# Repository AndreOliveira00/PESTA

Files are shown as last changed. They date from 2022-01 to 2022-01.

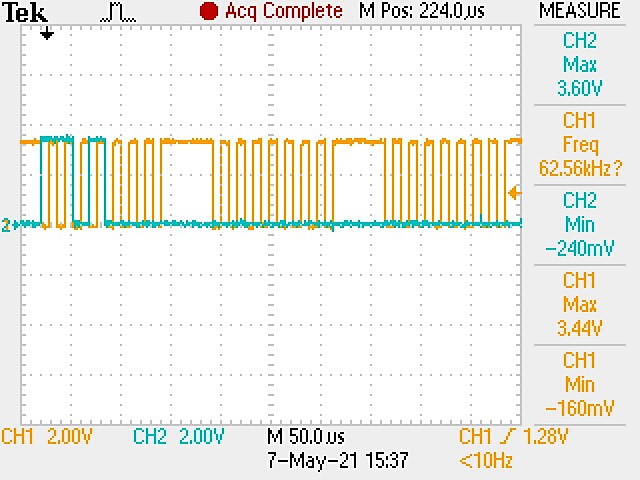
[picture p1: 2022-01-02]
Tests/SPI communication/MOSI/GetStatus_1.JPG

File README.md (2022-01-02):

# Skylight Control System
SISTEMA DE  CONTROLO DO MOVIMENTO DE UMA CLARABOIA

Este repositório contem o relatório e poster ilustrativo do projeto desenvolvido durante o estágio de fim de Licenciatura em Engenharia Eletrotécnica e de Computadores pelo Instituto Superior de Engenharia do Porto.
Contem ainda parte do código desenvolvido em: 
"...STM32CubeExpansion_SPN3\Projects\Multi\Examples\MotionControl\IHM03A1_ExampleFor1Motor" para controlo de todos os dispositivos incorporados na rede daisy chain.
Imagens ilustrativas da PCB final, o seu desenvolvimento associado e alguns testes efetuados para validação da comunicação SPI, teste de circuitos, respostas temporais, EMI e obtenção de constantes motoras.
Preço do desenvolvimento das duas PCBs associadas

RESUMO DO PROJETO:

O projeto apresentado neste documento consiste num sistema embebido para controlo de abertura e fecho de uma claraboia incorporada no tejadilho dos autocarros. A solução desenvolvida procurou a adaptabilidade a diferentes veículos, pelo que permitirá o controlo por parte do utilizador, sem maiores dificuldades, seguindo assim o conceito de Smart City.
O sistema visa a robustez sendo implícito a implementação das boas práticas Electromagnetic compatibility (EMC) e cumpridor da norma UNECE R10 no momento de dimensionamento do hardware associado. Os testes ao sistema desenvolvido foram feitos num laboratório isolado, com alimentação de uma bateria externa, com recurso a um analisador de espetro e sondas EMC.
O movimento rotativo do motor passo a passo NEMA 23 encontra-se acoplado com uma engrenagem módulo 1,5 capaz de elevar a estrutura por 7 cm. Este movimento é visível nos dois extremos da claraboia com auxílio de dois motores, sendo esta estrutura rígida.
O dispositivo de controlo principal é constituído por um microcontrolador Advanced RISC Machine (ARM) Cortex M4 de 32 bits, o STM32F401RET6 baseado numa arquitetura Reduced Instruction Set Computer (RISC), responsável por controlar os dois drivers junto 
dos referidos motores. Estes drivers incorporam um dispositivo de comando das fases, o powerSTEP01, com controlo programável através de Serial Peripheral Interface (SPI).
A comunicação entre o dispositivo principal e os drivers é feita através do protocolo de comunicação SPI segundo uma topologia em daisy chain atuando este primeiro como mestre e os restantes como escravos. Adicionalmente foi alvo de estudo a necessidade de 
implementação de uma comunicação RS-485 entre os dois escravos fruto de um sistema funcional num ambiente sujeito a ruído eletromagnético.

Para outros esclarecimentos contacte pelo email 1181045@isep.ipp.pt.

Notas:
  O desenvolvimento do software foi feito em: "...STM32CubeExpansion_SPN3\Projects\Multi\Examples\MotionControl\IHM03A1_ExampleFor1Motor"

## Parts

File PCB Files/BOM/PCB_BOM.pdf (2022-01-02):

# Bill of Materials

2175 Salk Avenue
Project Title: Bill of Materials for PCB Document [PCB2.PcbDoc] | Suite 200
Project File Name: Claraboia.PrjPcb | Carlsbad, CA 92008
Assembly Variant: None | USA
Part Number | Description | Designator | Manufacture | Manufacture Part Number | Supplier | Supplier Part Number | Supplier Unit Price | Quantity
S8B-EH_LF__SN_ | Conector Femea 1*8 90 graus | 485-1 | | | | | | | 1
CMP-02366-000003-1 | CONN MOD JACK 8P8C R/A UNSHLD | 485-2, 485-4 | | | | | | | 2
S8B-EH_LF__SN_ | Conector Femea 1*8 90 graus | 485-3 | | | | | | | 1
CMP-2100-03601-2 | CAP CER 0.1UF 50V X7R 0603 | C1, C2, C3, C4, C6, C9, C16, C17, C18, C19, C20, C21, C22, C23, C24, C36, C37, C39 | | | | | | 18
CMP-06035-019733-1 | Cap Ceramic 4.7uF 50V X5R ±10% SMD 0805 +85°C Emboss T/R | C5, C10, C44 | | | | | | | 3
CMP-2000-07203-1 | Tantalum Surface Mount Capacitor, 4.7 uF, +/- 20%, 50 V, -55 to 125 degC, 2-Pin SMD, RoHS, Tape and Reel T491D475M050AT | C7 | | | | | | | 1
CMP-06035-005015-1 | Chip Multilayer Ceramic Capacitors for General Purpose, 0805, 10uF, X5R, 15%, 10%, 50V GRM21BR61H106KE43K | C8 | | | | | | | 1
CMP-2006-02448-10603 | | C11, C12 | | | | | | | 2
CMP-2006-04264-1 | | C13, C14, C42, C43 | | | | | | | 4
CMP-1035-02737-2CAP CER 1UF 16V X5R 0603 CMP-0687-00076-1 | Aluminum Electrolytic Capacitor, UD Series, Low Impedance, 68 uF, 50 V, + / -20%, -55 to 105 degC, Chip Type, 8 x 10 mm D x L, Pb-Free, Reel UUD1H680MNL1GS | C15 C25, C26 | | | | | | | 1 2
EEU-FC1H680B | Capacitor Polarised | C27, C28 | | 2
CMP-1036-04552-2 | CAP CER 0.22UF 50V X7R 0805 | C29, C30, C31, C32, C33, C40 | | 6
CMP-13271-004199-1 | CL21 Series 0805 47nF 50V ±5% Tolerance X7R Multilayer Ceramic Chip Capacitor | C34 | | 1
CMP-2006-02821-1470 nF | | C35, C38 | | 2
T495A226K006ATE500 | Capacitor Polarised 22 uF TANT | C41 | | 1
CMP-0548-00185-2 | Transient Voltage Suppressor, 6.40 to 231 V, 30 V Stand-off Voltage, Bi-Directional, -55 to 155 degC, 2-pin DO-214AC, Pb-Free, Tape and Reel | D1, D3, D5, D8, D9, D10, D11, D14, D15, D16, D17, D18, D19, D30, D31 | 15
BAT760Q-7 | No Description Available | D2, D4, D6 | | 3
CMP-1426-00009-1 | SMD mono-color Chip LED, WL-SMCW, Bright Green | D7, D27 | | 2
CMP-1426-00012-1 | SMD mono-color Chip LED, WL-SMCW, Yellow | D12, D13, D20, D21, D22, D23 | | 6
CMP-2000-05915-2 | DIODE ARRAY SCHOTTKY 30V SOT23-3 | D24 | | 1
CMP-02539-000007-1 | DIODE SCHOTTKY 100V 150MA SOD123 | D25, D26 | | 2
CMP-1426-00011-1 | SMD mono-color Chip LED, WL-SMCW, Red | D28, D29 | | 2
CMP-1060-00535-1 | Zener Voltage Regulator, 500 mW, 2-Pin SOD-123, Pb-Free, Tape and Reel | D32 | | 1
MFU1206FF00500P100 Fuse | | F1 | | 1
MMZ1608S601ATD25 Ferrite Bead CMP-0225-00066-1 | Radial Leaded Wire Wound Inductor WE-TI, L = 4700 µH 7447721047 | FB1 L1 | | 1 1
P78E03-1000 | Connector | P1 | 1
M50-3530642 | Connector | P2 | 1
OSTYK42106030 CMP-1502-01064-1 | Connector THT Vertical Pin Header WR-PHD, Pitch 2.54 mm, Single Row, 4 pins | P3 P4 | 1 1
5-146254-8 | Connector | P5 | | 1
CMP-2000-05537-1 | Male Header, Pitch 2.54 mm, 1 x 2 Position, Height 11.7 mm, Tail Length 3.56 mm, 0 to 75 degC, RoHS, Bulk | P6 | | 1
CMP-2000-05537-1 | Male Header, Pitch 2.54 mm, 1 x 2 Position, Height 11.7 mm, Tail Length 3.56 mm, 0 to 75 degC, RoHS, Bulk | P7 | | 1
CMP-02550-000125-1 | MOSFET P-CH 40V 7.2A 8SOIC | Q1 | | 1
CMP-2100-03667-1 | Chip Resistor, 0 Ohm, +/-5%, 0.1 W, -55 to 155 degC, 0603 (1608 Metric), RoHS, Tape and Reel | R1, R3, R14, R15, R19, R21, R25, R40, R41 | | 9
CMP-2100-03667-1 | Chip Resistor, 0 Ohm, +/-5%, 0.1 W, -55 to 155 degC, 0603 (1608 Metric), RoHS, Tape and Reel | R2, R4, R16, R17, R24, R35, R36, R39, R43, R44, R49, R50, R51, R52, R54, R55, R56, R59, R60, R61, R63, R65, R66, R67, R68, R69, R70 | 27
CMP-2000-00070-1 Resistor, 10 kOhm, +/- 5%, 100 mW, -55 to 155 degC, CMP-2000-05022-1 0603 (1608 Metric), RoHS, Tape and Reel | | R5, R20, R22 R6, R7, R10, R11, R12, R13, R18, R23, R26, R28, R29, R30, R31, R32, R37, R64 | 16 | 3
CMP-2100-03667-1 | Chip Resistor, 100 Ohm, +/-5%, 0.1 W, -55 to 155 degC, 0603 (1608 Metric), RoHS, Tape and Reel | R8, R9, R27, R38, R53, R58 | 6
CMP-2000-03816-5 | Chip Resistor, 4.7 kOhm, Jumper, 100 mW, -55 to 155 degC, 0603 (1608 Metric), RoHS, Tape and Reel | R33 | 1
CMP-2000-00042-1 | Chip Resistor, 330 Ohm, +/- 5%, 0.1 W, -55 to 155 degC, 0603 (1608 Metric), RoHS, Tape and Reel | R34, R42, R46, R48 | 4
CMP-2000-00055-10603 | RES 0.05 OHM 1% 1W | R45, R47 | 2
CMP-2000-07420-2 | 2512, RES 0.1 OHM 1% 2W 2512 | R57, R62 | 2
CMP-03402-000005-1 | SWITCH TACTILE SPST-NO 0.05A 24V | SW1, SW2 | 2
CMP-2000-05182-1 | Test Point, White, 1-Pin THD, RoHS, Bulk | TP1, TP2, TP3, TP4, TP5, TP6, TP7 | 7
NSI50010YT1G | Diode | U1, U3 | 2
CMP-2000-07401-1 | Low Input Current, Phototransistor Output, 80 V, 170 mW, -55 to 110 degC, 4-Pin SOP, RoHS, Tape and Reel | U2, U4 | 2
SN65HVD70DGS | Integrated Circuit | U5 | 1
CMP-12105-000004-1 | IC MCU 32BIT 512KB FLASH 64LQFP | U6 | 1
MAX3293AUT+T MAX3280EAUK_V+TIntegrated Circuit | Integrated Circuit | U9, U10 U7, U8 | 2 2
POWERSTEP01 | No Description Available | U11 | 1
CMP-2000-05036-1 | Low Frequency Crystal, 32.768 KHz, 6 pF, +/- 20 ppm, -40 to 85 degC, 4-Pin SMD, RoHS, Tape and Reel | X1 | 1
CMP-1749-00003-1 | Resistance Weld Thru-Hole Crystal, 16 MHz, -20 to 70 degC, 2-Pin THD, RoHS, Bulk | X2, X3 | 2
| $0,00 184
Approved | | Notes

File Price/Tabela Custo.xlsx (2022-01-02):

 |  | MCU+SLAVE |  |  |  |  |  |  | SLAVE
Manufacturer 1 | Part#1 | DESCRIÇÃO | QUANTIDADE |  | PU (€) | TOTAL (€) | Manufacturer 1 | Part#1 | DESCRIÇÃO | QUANTIDADE |  | PU (€) | TOTAL (€)
 | 7447721047 | Bobine 4,7 mH | 1 |  | 0.575 | 0.575 |  |  | Bobine 4,7 mH | 1 |  | 0.575 | 0.575
YAGEO | CC0603KRX5R7BB105 | Condensador Cerâmica 4,3 pF / 50 V 0402 | 2 |  | 0.013 | 0.026 |  | MAX3280EAUK/V+T | Condensador Cerâmica 47 nF / 50 V 0805 | 1 |  | 0.0975 | 0.0975
 | CC1206KKX5R9BB106 | Condensador Cerâmica 47 nF / 50 V 0805 | 1 |  | 0.0975 | 0.0975 |  |  | Condensador Cerâmica 100 nF 50 V 0603 | 6 |  | 0.037 | 0.222
YAGEO | CC0603KRX7R9BB104 | Condensador Cerâmica 100 nF 50 V 0603 | 16 |  | 0.037 | 0.592 |  |  | Condensador Cerâmica 220 nF / 50 V 0805 | 6 |  | 0.058 | 0.348
 |  | Condensador Cerâmica 220 nF / 50 V 0805 | 6 |  | 0.058 | 0.348 |  |  | Condensador Cerâmica 470 nF / 25 V 0603 | 2 |  | 0.057 | 0.114
 | CL10B105KO8NFNC | Condensador Cerâmica 470 nF / 25 V 0603 | 2 |  | 0.057 | 0.114 |  |  | Condensador Cerâmica 4,7 μF / 50 V 0805 | 2 |  | 0.11 | 0.22
YAGEO | CC1206KKX7R8BB475 | Condensador Cerâmica 1 μF / 16 V 0603 | 1 |  | 0.018 | 0.018 |  |  | Condensador Cerâmica 10 μF / 50 V 0805 | 1 |  | 0.091 | 0.091
 | 885012207102 | Condensador Cerâmica 4,7 μF / 50 V 0805 | 3 |  | 0.11 | 0.33 |  |  | Condensador Eletrolítico Tântalo 4,7 μF / 50 V 2917 | 1 |  | 0.3815 | 0.3815
 | CC0603JRX7R8BB474 | Condensador Cerâmica 10 μF / 50 V 0805 | 1 |  | 0.091 | 0.091 |  |  | Condensador Eletrolítico Tântalo 22 uF / 6V3 | 1 |  | 0.422 | 0.422
 | UUD1H680MNL1GS | Condensador Eletrolítico Tântalo 4,7 μF / 50 V 2917 | 1 |  | 0.3815 | 0.3815 |  |  | Condensador Eletrolítico 68 μF / 50 V 8*10 | 2 |  | 0.341 | 0.682
 |  | Condensador Eletrolítico Tântalo 22 uF / 6V3 | 1 |  | 0.422 | 0.422 |  |  | Conector Fêmea RJ45 | 1 |  | 0.561 | 0.561
 | T495A226K006ATE500 | Condensador Eletrolítico 68 μF / 50 V 8*10 | 2 |  | 0.341 | 0.682 |  |  | Conector Macho 1*2 com bloqueio | 1 |  | 0.12 | 0.12
 | RJHSE-5080-ND | Conector Fêmea RJ45 | 1 |  | 0.561 | 0.561 |  |  | Díodo Schottky BAR43 | 1 |  | 0.025 | 0.025
 | 67996-416HLF | Conector Macho 1*16 | 1 |  | 0.363 | 0.363 |  |  | Díodo Schottky BAT46 | 2 |  | 0.105 | 0.21
Header 2 | 61300411121 | Conector Macho 1*4 | 1 |  | 0.0785 | 0.0785 |  |  | Díodo Schottky BAT760Q-7 | 1 |  | 0.12 | 0.12
 | 22272021 | Conector Macho 1*2 com bloqueio | 2 |  | 0.12 | 0.24 |  |  | Díodo Zener 15 V | 1 |  | 0.084 | 0.084
 | M50-3530642 | Conector Macho 1*6 | 1 |  | 0.015 | 0.015 |  |  | Driver de motores PowerSTEP01 | 1 |  | 6.65 | 6.65
Abracon | ABS25-32.768KHZ-6-T | Cristal ABS25-32.768KHZ-6-T | 1 |  | 0.7 | 0.7 |  |  | Ferrite 350 mΩ /500 mA 0603 | 1 |  | 0.026 | 0.026
 | 2156-BAR43-ND | Díodo Schottky BAR43 | 1 |  | 0.025 | 0.025 |  |  | Díodo Zener 15 V | 1 |  | 0.084 | 0.084
 | BAT46W-E3-08 | Díodo Schottky BAT46 | 2 |  | 0.105 | 0.21 |  |  | Interruptor SMD 6x6 mm | 1 |  | 0.1 | 0.1
 | BAT760Q-7DICT-ND | Díodo Schottky BAT760Q-7 | 3 |  | 0.12 | 0.36 |  |  | LED Amarelo SMD | 4 |  | 0.084 | 0.336
 | 497-15441 | Díodo Zener 15 V | 1 |  | 0.084 | 0.084 |  | T495A226K006ATE500 | LED Verde SMD | 2 |  | 0.084 | 0.168
 |  | Driver de motores PowerSTEP01 | 1 |  | 6.65 | 6.65 |  |  | LED Vermelho SMD | 2 |  | 0.084 | 0.168
 |  | Driver MAX3293 | 2 |  | 0.97 | 1.94 |  |  | MOSFET canal P SI4447ADY-T1-GE3 | 1 |  | 0.27 | 0.27
Tai-tech | MMZ1608S601ATD25 | Ferrite 350 mΩ /500 mA 0603 | 1 |  | 0.026 | 0.026 |  |  | Receivers MAX3280E | 2 |  | 0.71 | 1.42
 |  | Fusível 3,5A | 1 |  | 0.19 | 0.19 |  |  | Resistência 0 Ω 0,1 W 0603 | 2 |  | 0.003 | 0.006
 |  | LED Amarelo SMD | 6 |  | 0.084 | 0.504 |  |  | Resistência 0,1 Ω / 2 W 2512 | 2 |  | 0.213 | 0.426
 |  | LED Driver NSV50010YT1G | 2 |  | 0.22 | 0.44 |  |  | Resistência 47 Ω / 0,1 W 0603 | 1 |  | 0.0085 | 0.0085
 |  | LED Verde SMD | 2 |  | 0.084 | 0.168 |  |  | Resistência 100 Ω / 0,1 W 0603 | 4 |  | 0.005 | 0.02
 |  | LED Vermelho SMD | 2 |  | 0.084 | 0.168 |  |  | Resistência 330 Ω 0,1 W 0603 | 4 |  | 0.006 | 0.024
 |  | Microcontrolador STM32F401RET6 | 1 |  | 4.38 | 4.38 |  |  | Resistência 4,7 kΩ / 0,1 W 0603 | 1 |  | 0.005 | 0.005
 |  | MOSFET canal P SI4447ADY-T1-GE3 | 1 |  | 0.27 | 0.27 |  |  | Resistência 10 kΩ / 0,1 W 0603 | 14 |  | 0.003 | 0.042
wealthmetal | TL1105CF250Q | Interruptor SMD 6x6 mm | 2 |  | 0.1 | 0.2 |  |  | Resistência 39 kΩ 0,1 W 0603 | 2 |  | 0.013 | 0.026
 |  | Optocoupler VOM618A-3T | 2 |  | 0.17 | 0.34 |  |  | Test Point | 5 |  | 0.113 | 0.565
 |  | Regulador P78E03-1000 | 1 |  | 2.15 | 2.15 |  |  | Transceiver SN65HVD70D | 1 |  | 1.39 | 1.39
YAGEO | RC0603JR-070RL | Resistência 0 Ω 0,1 W 0603 | 8 |  | 0.003 | 0.024 |  |  | TVS SMAJ30CA-E3/61 | 9 |  | 0.12 | 1.08
 | PCS2512DR1000ET | Resistência 0,1 Ω / 2 W 2512 | 2 |  | 0.213 | 0.426 |  |  |  |  | Total (€) |  | 17.09
 | RC0603JR-0710KL | Resistência 47 Ω / 0,1 W 0603 | 3 |  | 0.0085 | 0.0255
 |  | Resistência 100 Ω / 0,1 W 0603 | 4 |  | 0.005 | 0.02
 |  | Resistência 330 Ω 0,1 W 0603 | 4 |  | 0.006 | 0.024
 |  | Resistência 4,7 kΩ / 0,1 W 0603 | 1 |  | 0.005 | 0.005
 |  | Resistência 10 kΩ / 0,1 W 0603 | 16 |  | 0.003 | 0.048
 |  | Resistência 39 kΩ 0,1 W 0603 | 2 |  | 0.013 | 0.026
 |  | Test Point | 7 |  | 0.113 | 0.791
 |  | Transceiver SN65HVD70D | 1 |  | 1.39 | 1.39
 |  | TVS SMAJ30CA-E3/61 | 11 |  | 0.12 | 1.32
 |  |  |  | Total (€) |  | 27.84

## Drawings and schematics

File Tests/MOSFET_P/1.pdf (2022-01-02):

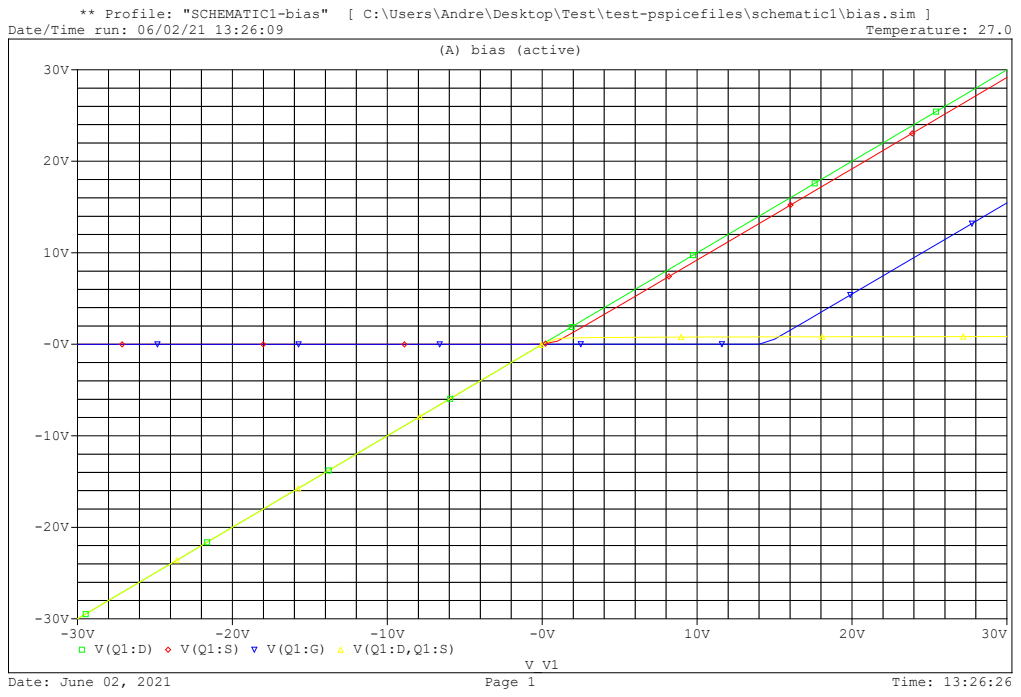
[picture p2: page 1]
Temperature: 27.0; Date: June 02, 2021; Page 1; Time: 13:26:26; (A) bias (active)

** Profile: "SCHEMATIC1-bias" [ C:\Users\Andre\Desktop\Test\test-pspicefiles\schematic1\bias.sim ]

Date/Time run: 06/02/21 13:26:09

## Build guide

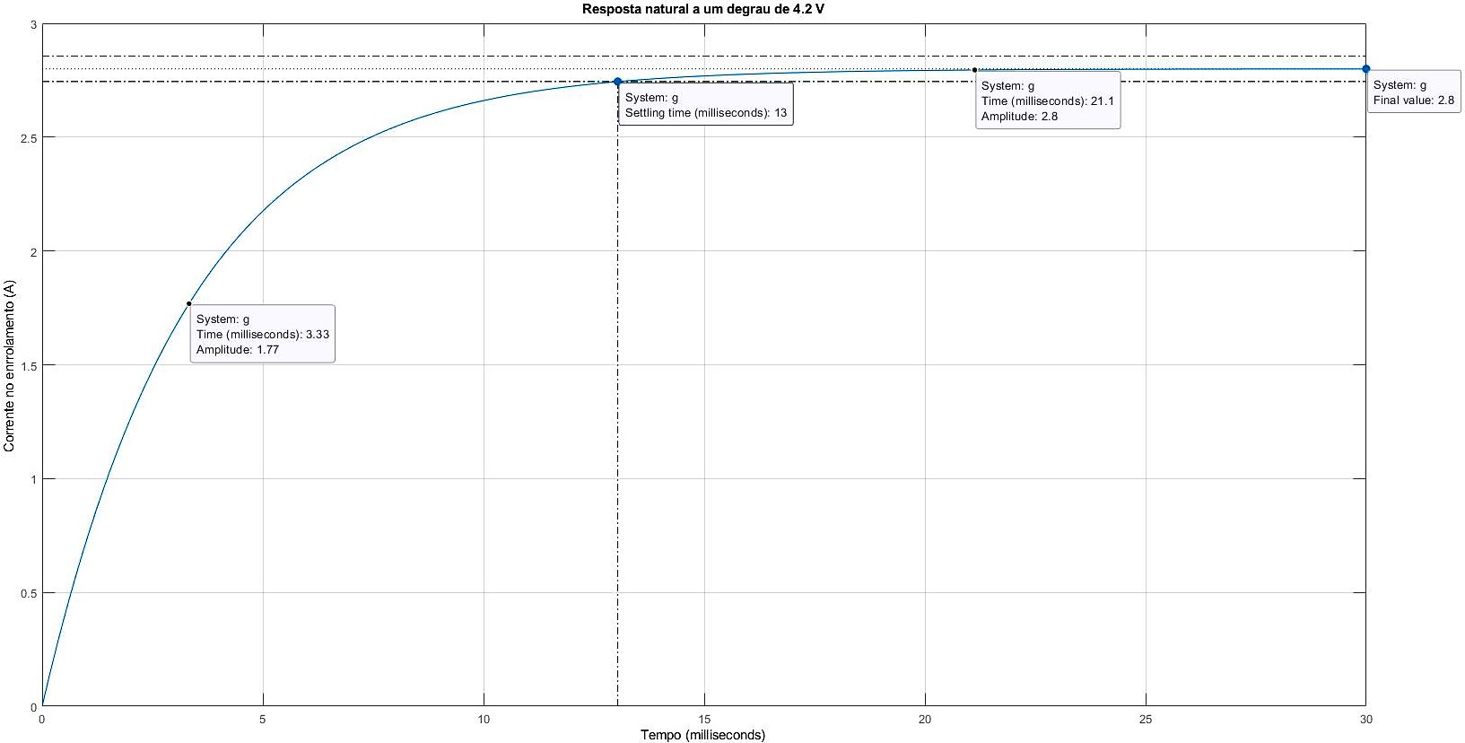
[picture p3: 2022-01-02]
Tests/Step Response-Matlab/Resposta ao degrau.jpg

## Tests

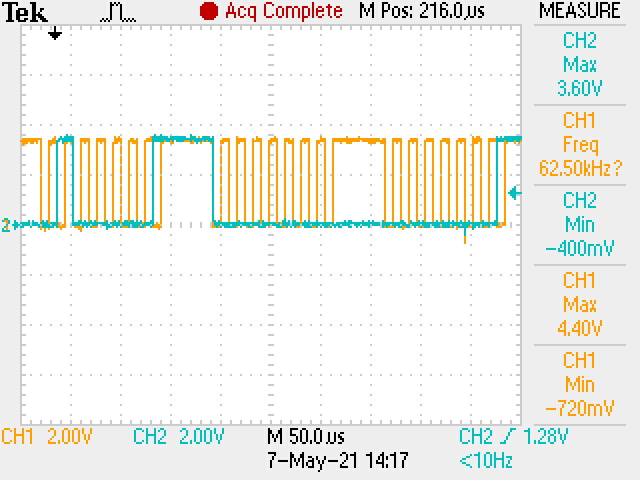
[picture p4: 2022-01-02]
Tests/SPI communication/MOSI/Move(0, FORWARD, STEEPS)_1.JPG

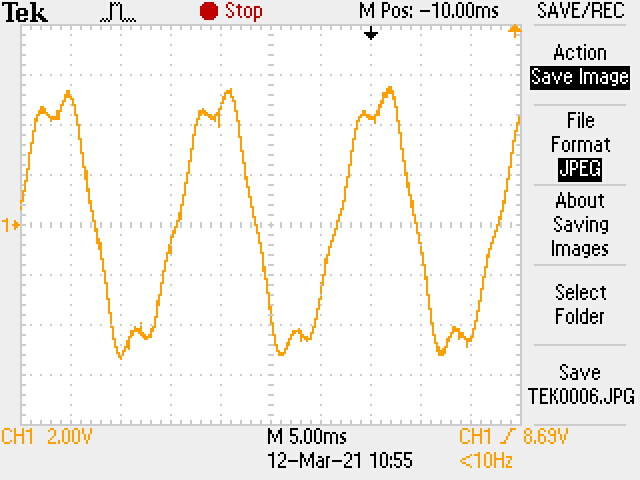
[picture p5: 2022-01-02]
Tests/Ke constant/75_rpm.JPG

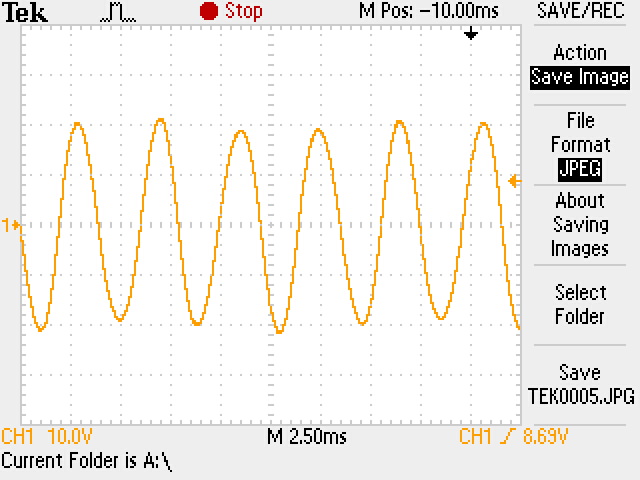
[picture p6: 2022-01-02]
Tests/Ke constant/300_rpm.JPG

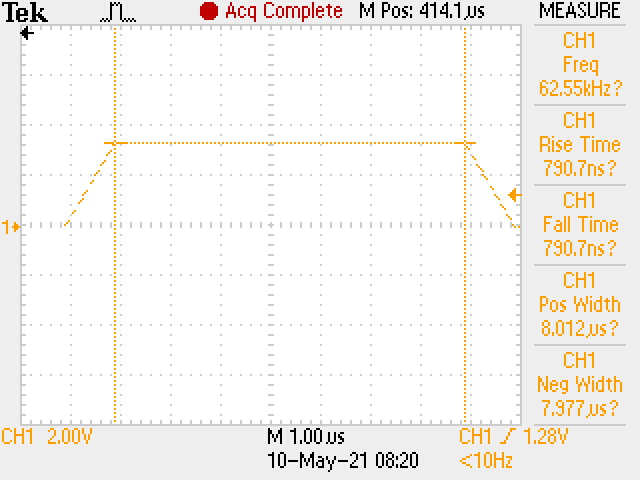
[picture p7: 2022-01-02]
Tests/SPI communication/CLK/CLK_62.5_kHz_On_time.JPG

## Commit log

2022-01-02 Create Board Core and Libraries
2022-01-02 Delete STM32CubeExpansion_SPN3_Code.zip
    Diretório alterado -> Board Core and Libraries
2022-01-02 Update Project
    [Claraboia.PrjPcb, Inputs.SchDoc, MCU_F401RE.SchDoc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]
